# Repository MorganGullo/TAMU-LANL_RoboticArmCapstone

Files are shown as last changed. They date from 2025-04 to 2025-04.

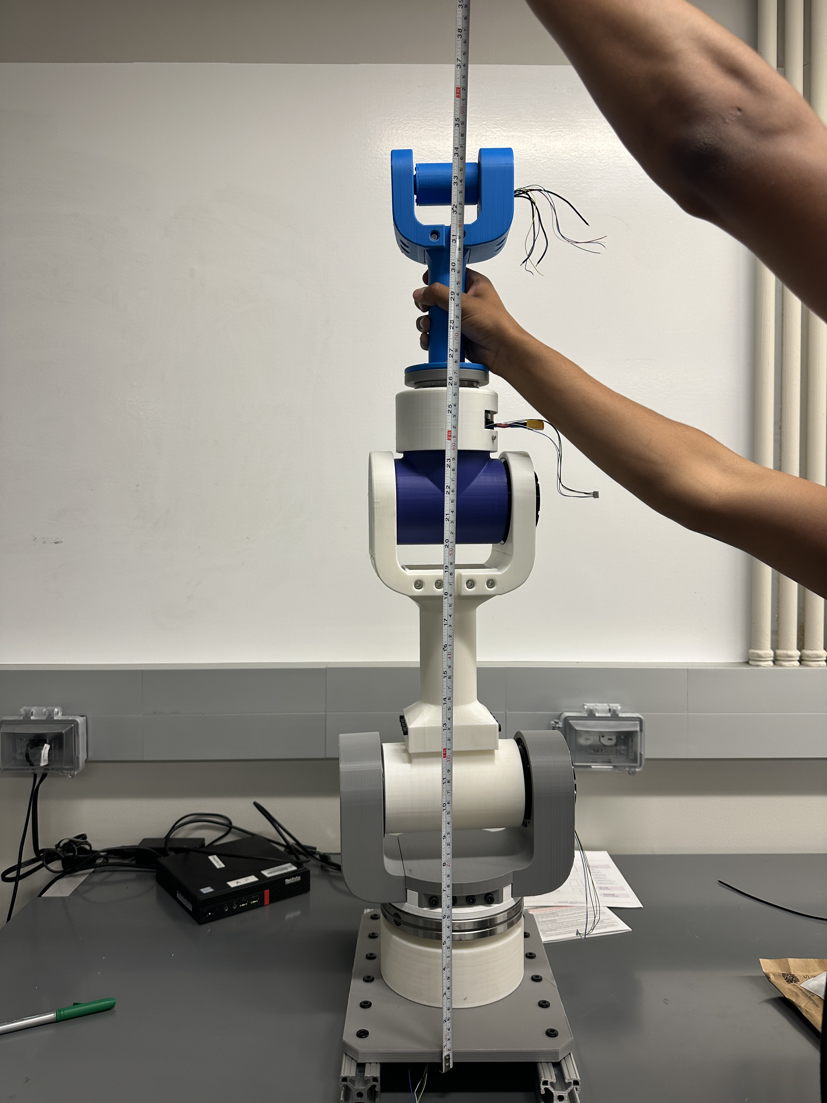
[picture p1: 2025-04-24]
Photos/Vertical Extension.JPG

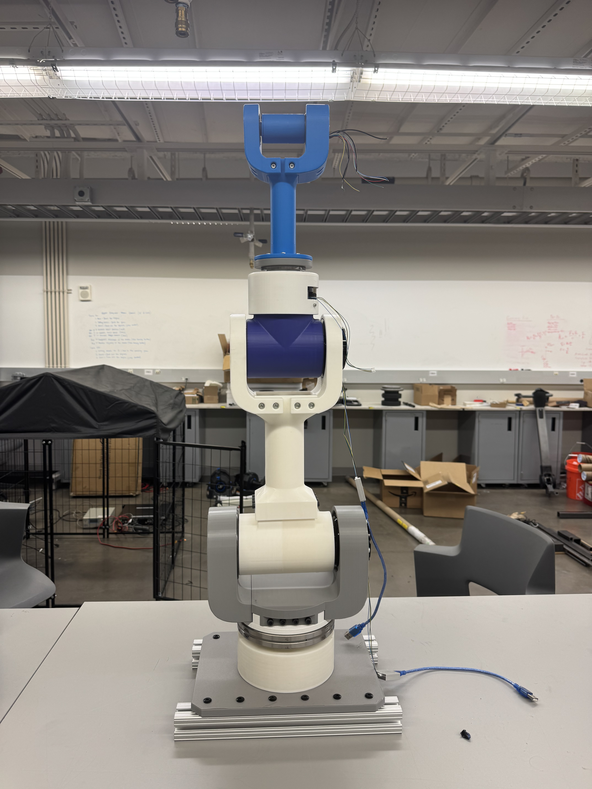
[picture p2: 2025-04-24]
Photos/Vertical Extension.jpeg

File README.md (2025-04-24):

# TAMU LANL Human Robotic Arm Capstone
Texas A&M University Mechanical Engineering Senior Design Project in partnership with Los Alamos National Laboratory to create a Human Robotic Arm Attachment

<p align="center">
  

<p align="center">


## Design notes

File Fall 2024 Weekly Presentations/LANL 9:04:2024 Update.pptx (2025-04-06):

## LANL Team Update 9/3/2024 Izzy Baumler, Dalton Boeckmann, Morgan Gullo, Jade Waldron

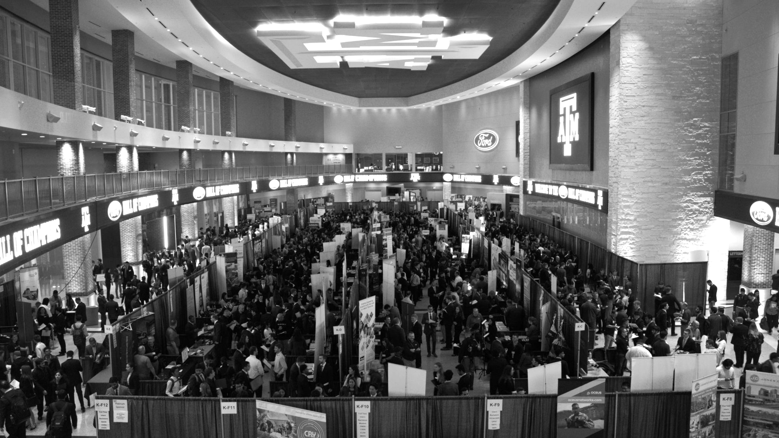
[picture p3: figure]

## Weekly Task Updates

Continuing Research for DR1 Report
- After talking with Dr.Tsenn we have divided up the DR1 research topics
  - Jade - Arm attachments and storage
  - Morgan - Arm attachments and storage
  - Dalton - Dynamic behavior of control arm
  - Izzy - Electrical behavior of control arm
- Meeting with Shuangyu Xie delayed to next tuesday to discuss arm attachment for her weed removal project
- Creating our list of people we want to interview

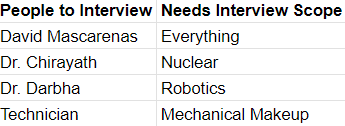
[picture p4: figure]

## Weekly Task Updates

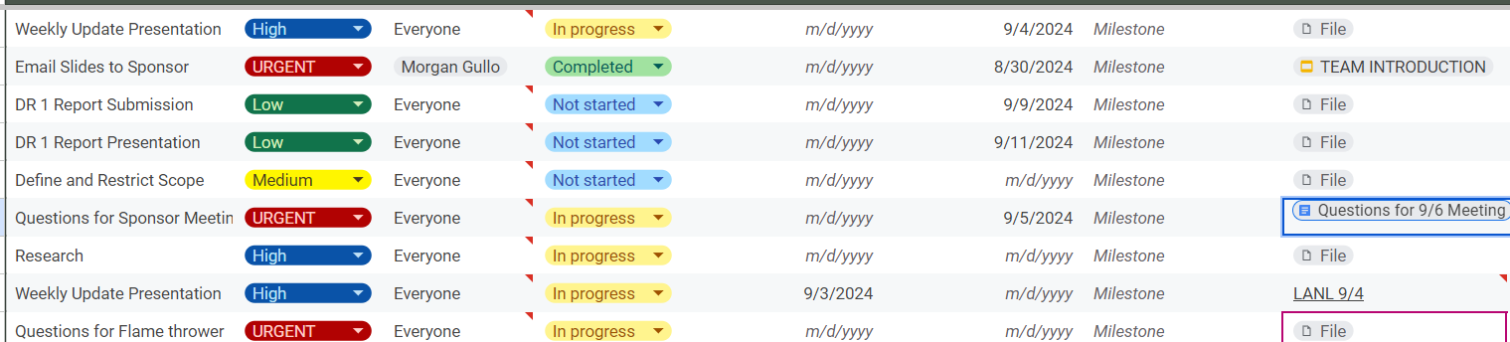
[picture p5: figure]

## Upcoming Week

- Meeting with our sponsor on 9/6 at 1 PM
  - We have prepared questions for him to hopefully answer
- Conducting Interviews for Needs Analysis
- Finalizing and Submitting our DR1 Reports
- Meeting with Shuangyu Xie 9/10

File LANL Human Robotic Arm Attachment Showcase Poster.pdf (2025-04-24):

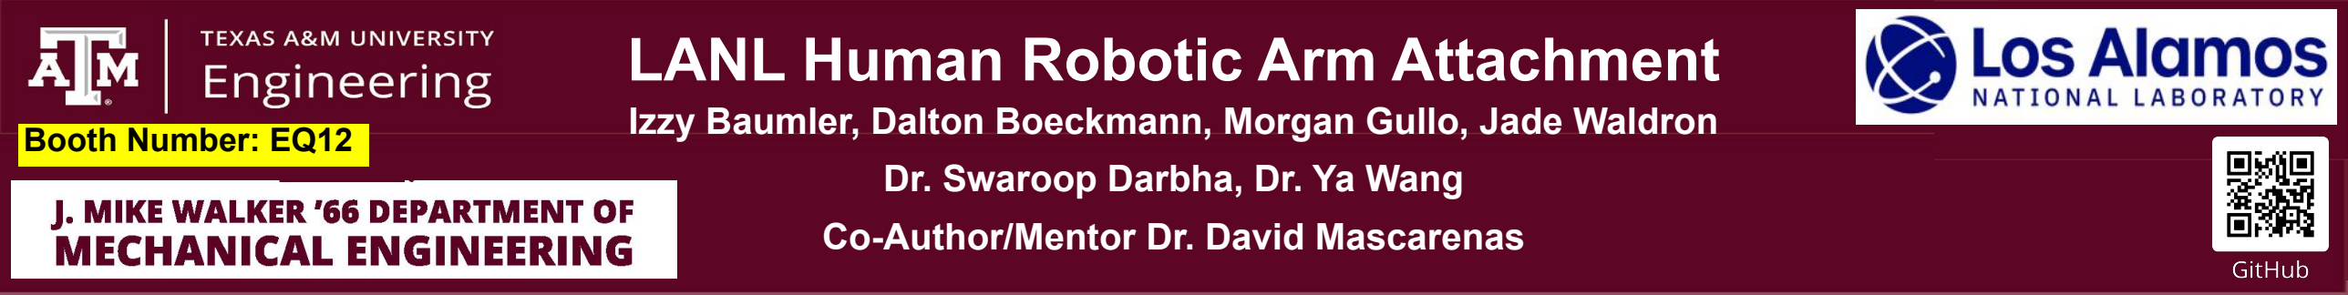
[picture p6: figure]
LANL Human Robotic Arm Attachment; Dr. Swaroop Darbha, Dr. Ya Wang; Co-Author/Mentor Dr. David Mascarenas; Booth Number: EQ12

## Izzy Baumler, Dalton Boeckmann, Morgan Gullo, Jade Waldron

References

[1] Department of Energy. "Hanford Site Overview." U.S. Department of Energy, 2021, https://ecology.wa.gov/waste-toxics/nuclear-waste/hanford-cleanup/hanford-overview.
[2] D. Herman et al., “Evaluation of Technology for Dry Retrieval of Tank Waste,” OSTI OAI (U.S. Department of Energy Office of Scientific and Technical Information), Feb. 2024, doi: https://doi.org/10.2172/2319155.
Acknowledgements

Thank you Dr. David Mascarenas, Dr. Swaroop Darbha, Dr. Ya Wang, RPS, RAD Lab

There is a need for a technology that has 5 degrees-of-freedom and can move through its full range of motion in four degrees-of-freedom of at least 1 Hz.
- The Hanford Site in Washington stores 56+ million gallons of radioactive waste in deteriorating underground tanks. [1]
- Many tanks exceed their lifespan capacity and pose serious environmental and safety risks
- Key challenge: Solidified waste is hard to remove due to small access ports (~1 ft diameter) and extreme radiation levels [2]
- Existing robotic solutions lack the mobility, speed, and/or reliability to operate in confined, hazardous conditions
- Our goal: Design a 5 degrees-of-freedom robotic arm to be eventually mounted on a quadruped robot for effective remote cleaning of nuclear waste tanks

Identified Customer Needs - Derived from interviews with Engineers at Savannah River
National | Laboratory, | supplemental | survey
responses (Robotics Experts), and our sponsor

Only Survey Responses are shown in pie chart*
Design Requirements
- Total system weight: ≤ 14 kg (~30 lbs)
- Minimum Joint Torque (to hold itself up):
- J1 & J2 > 10 Nm, J3 & J4 > 2 Nm
- Reach: ≥ 0.67 meters
- Motion Frequency: ≥ 1 Hz (J1-J4)

Joint 1 SolidWorks Assembly:

Joint 2 SolidWorks Assembly:

Joint 3 SolidWorks Assembly:

The testing process for the robotic arm focused on motor performance under position, speed, and torque control, with testing performed both individually and integrated within the system.
J1 - J4 motors exceeded the target motion frequency of 1 Hz and demonstrated accurate responsiveness to positional commands (0° -
180°). Full-extension load testing on joints J2 and J3 confirmed the arm could sustain torque demands to hold itself up without structural failure, validating the motor selection and mechanical integrity of the design.

Joint 4 SolidWorks Assembly:

Joint 5 SolidWorks Assembly:

Component Selection
- Linkages: 3D printed PLA
- Motors: CubeMars Brushless DC & Gimbal
- Controls: R-link & Upper Computer Software (USB to serial port communication)
- Power Supply: B&K Precision 9115B (80V-60A)
- M6 - M2.5 Various Length Fasteners
Trade Offs:
- Selected Modular Design Instead of Integrated
- Prioritized Speed Instead of Accuracy

Cost Accounting and Cost Model
- Total Spent on Capstone Budget: $4,330
- Total Project Cost Model: $8,370
Our sponsor contributed significantly by providing critical components, including J3 and J4 motors (approx. $700 each) and a power supply (approx. $2,550). The team also incurred an unexpected customs fee of around $500 during motor importation. Future Work & Lasting Impact
- Implement Arduino-to-CAN communication for streamlined multi-motor control and reduced wiring complexity
- Integrate wiring to enable full range of motion
- Develop gimbal-based control for the J5 motor
- The project intends to support ongoing research and spot robot integration
Joint | Calculated Torque (N-m) | Actual Torque (N-m)
J2 | 21.3 | 20
J3 | 3.7 | 2

J1 motor speed response during integrated testing. Verification confirms motion frequency at 1 Hz (6.26 rad/s). *

J1 motor positional response during integrated testing. Verification confirms accurate Position control for (0° - 180°).*

## Problem Statement & Project Motivation

## Customer Needs & Design Requirements

System Design Overview | Design Decisions & Trade Offs

## Testing & Validation

## Budget, Limitations, Impact & Future Work

Metric | Required Values | Verified Values | Units
Weight of the Arm | <14 | 11.88 | kg
Minimum Torque Output | 2-10 | 2-20 | Nm
Reach of Robotic Arm | >0.67 | 0.9 | m
System Mass Distribution | 0.209 | 0.132 | kg/cm
Frequency of Motion | 1 | 1 | Hz

Fully integrated torque testing at maximum extension, comparing the calculated values against the operational torque values to validate that the arm can successfully support itself at full reach. *

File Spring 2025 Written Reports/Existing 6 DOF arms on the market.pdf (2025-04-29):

# Existing 6 DOF arms in Industry

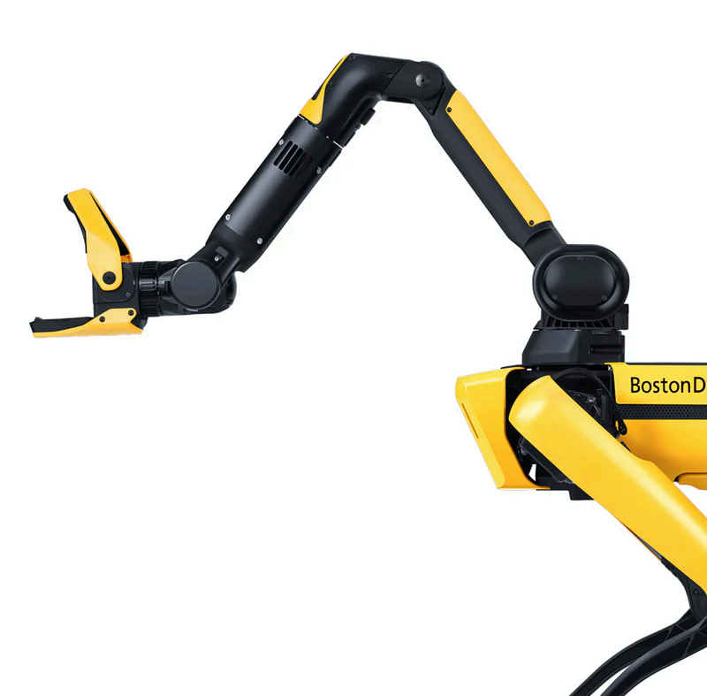
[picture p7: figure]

### Boston Dynamics Spot Arm

- Cost: $65,000
- Weight: 8 kg
- Payload Capability: ~11 kg
- Custom Proprietary BLDC Motors
- Reach ~ 984 mm

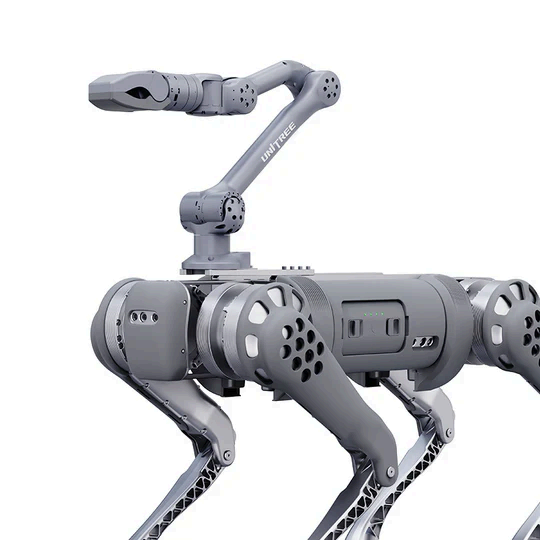
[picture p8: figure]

### Unitree Z1

- Cost: $16,000
- Weight: 4.3 kg
- Payload Capability: ~ 2 kg
- Custom Proprietary BLDC Motors
- Reach ~ 700 mm

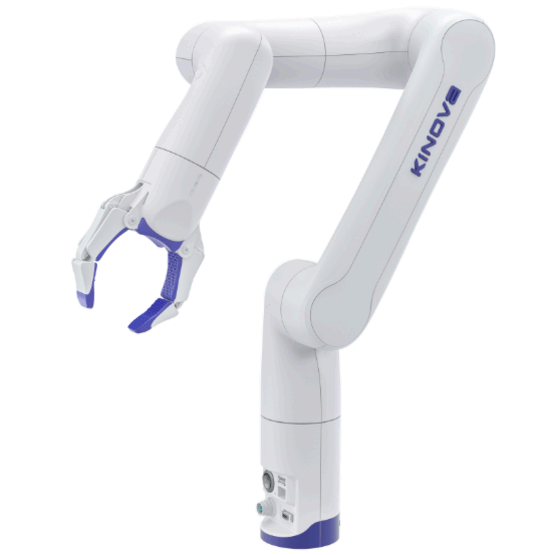
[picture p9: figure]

### Kinova Gen3 lite

- Cost: $13,500
- Weight: 5.4 kg
- Payload Capabilities: ~0.5 kg
- Custom Proprietary BLDC Motors
- Reach ~ 760 mm

# Existing 6 DOF arms in Industry

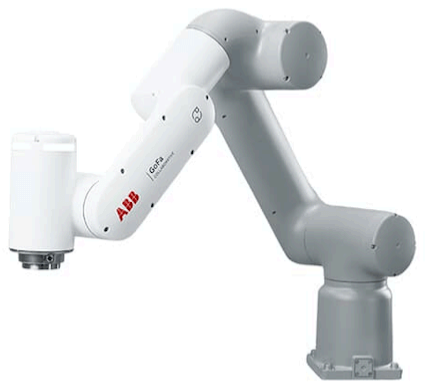
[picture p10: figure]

### ABB CRB15000 GoFa5

- Cost: $38,900
- Weight: 28 kg
- Payload Capabilities: ~5 kg
- Custom Proprietary BLDC Motors
- Reach ~ 1050 mm

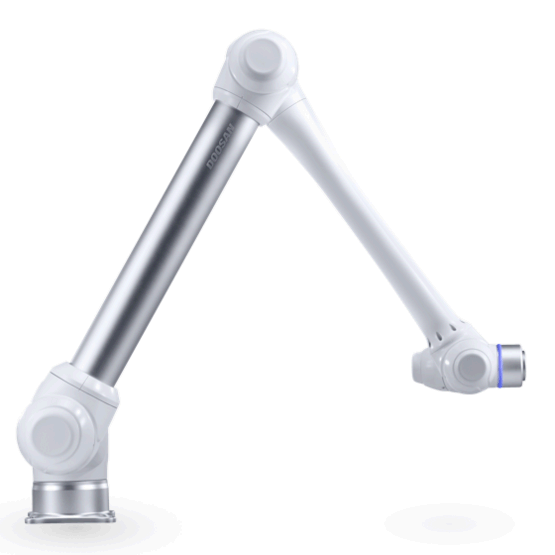
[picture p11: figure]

### Doosan M0617 Collaborative Robot

- Cost: $44,500
- Weight: 34.0 kg
- Payload Capabilities: ~6 kg
- Most likely Servo Motor (built in torque sensing)
- Reach ~ 1700 mm

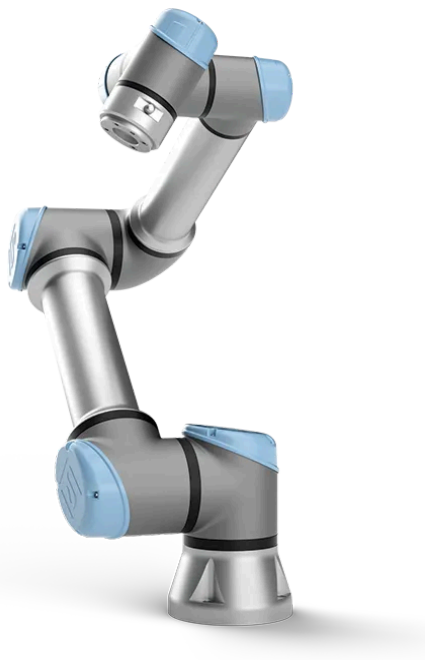
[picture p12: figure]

### Universal Robotics UR5e

- Cost: $36,000
- Weight: 18.4 kg
- Payload Capabilities: ~5 kg
- KBM Frameless AC Servo Motors
- Reach ~ 850 mm

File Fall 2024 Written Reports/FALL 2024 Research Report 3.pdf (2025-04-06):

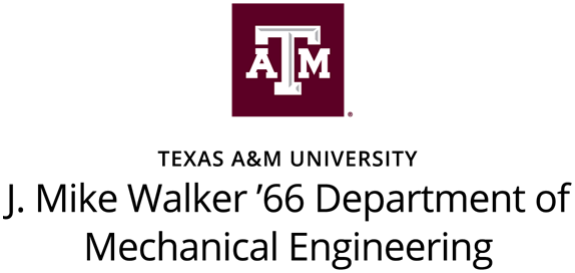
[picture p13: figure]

## Kinematic and Dynamic Considerations for the Design of a 7DoF Robotic Arm for Hazardous Waste Management

### September 4, 2024 Dr. Mascarenas Los Alamos National Laboratory By: Dalton Boeckmann

Glossary

Acronym | Definition
DOE | Department of Energy
LANL | Los Alamos National Laboratory
DoF | Degrees of Freedom
SNPS | Solution Neutral Problem Statement

Table of Contents

### 1. Introduction

The scope of this senior design team's project is to design an advanced robotic solution for hazardous waste removal at the Hanford Site in Washington State. The Hanford Site, among its 45-plus years of plutonium production, has generated more than 56 million gallons of mixed hazardous and radioactive waste. The storage tanks for this waste were designed with a shelf life of 25 years but have already outlived expectation; which has caused more than 68 tanks to be in critical condition. With this increasing issue Los Alamos National Laboratory (LANL) has imposed a design challenge for four mechanical engineering students at Texas A&M university to design a 7 Degree of Freedom (DoF) robotic arm that will attach to a quadruped robot and perform cleaning operations to help break up and remove solidified waste.
The main problem at the Hanford Site is how to address the containment and removal of the nuclear waste, that has already solidified into a crystallized-salt structure. The Department of Energy’s Environmental Impact Statement underlines the disastrous impact of every possible leak of these currently deteriorating tanks by again raising the degree of urgency for ingenious engineering solutions. Historically, the DOE has taken steps to stabilize the Hanford tanks by removing as much liquid waste from the tanks as possible to avoid leakage. [1]
However, recovering the remaining solidified waste is still a formidable technical task. These tanks were not originally designed for waste retrieval process, and the access points are only about one foot in diameter, which greatly restricts the size of equipment that can be used. Furthermore, the high radioactivity calls for remotely operated equipment that many times has failed under harsh conditions inside these tanks. All these challenges have pointed to the need for a solution that is more robust and efficient. The team has been tasked, under the guidance of Dr. David Dennis Lee Mascarenas from Los Alamos National Laboratory, with designing a 7-degreeof-freedom robotic arm attached to a quadruped robot to perform cleaning activities inside these hazardous waste tanks.
Dr. Mascarenas brings expertise in both robotics and environmental remediation needed to address engineering designs to help improve the harsh conditions inside these tanks. Therefore, the robotic arm proposed will be expected to break through the existing barriers of retrieving waste in a more efficient and safe way. This project targets minimizing the risk of further leaks with reduced potential environmental impact by improving the process of waste removal. This design review encompasses the background research done specifically on the design process of the 7 DoF robotic arm, the teams problem statement, and conclusions for future work on the project. First, the background research that follows provides foundational knowledge in current techniques on calculating the kinematic and dynamic behavior of industrial robots in hopes of using it for further application for our specific project.

### 2. Background

There is a great need to introduce design for a 7-DOF robotic arm to effectively meet the needs of expelling waste from hazardous tanks. In light of the success of this design, consideration of the analysis process of the mechanical capability of a 7-DOF arm should be taken into account. This background is necessary in order to provide the grounds where informed design decisions can be made, good control strategies can be initiated, and the integration of advanced technology can be attained.
The goal of this background research is to explain and define the process of analyzing the basic principles of kinematics and dynamics of a 7-DOF robotic arms. More specifically, this will set the grounds for: 1) how the robotic arms end effectors position is described relative to its base location, 2) how possible workspace is defined from these calculations, and 3) how various mathematical calculations are utilized to relate different joint operations and its effects on the endeffectors kinematic and dynamic characteristics. In order to do this, a review of technological developments and their applications in related industries will also be presented with the intent of explaining and applying different advances in robotics to the team’s design. Through this research, the team will gain a better understanding of the necessary design parameters taken into account for a 7-DOF robotic arm that can meet the demands of hazardous waste management cleanup process. Kinematics in robotics starts with analyzing the motion of the system without considering the forces causing these motions. For a 7-degree-of-freedom (7DOF) robot, understanding kinematics is crucial for determining how each joint movement affects the position and orientation of the robot's end-effector. The coordinate systems and reference frames attached to each link are fundamental for modeling a robot's geometry. The Denavit-Hartenberg (DH) convention is a widely-used method for defining these frames and the transformations between them. Denavit-Hartenberg (DH) convention is used to simplify the process of defining and calculating joint and link parameters. The DH convention is a method for assigning coordinate frames to each joint and link of a robot manipulator (see Appendix A). The final DH parameters are then used to form the homogeneous transformation matrices, which describe the position and orientation of the end-effector, in our case the cleaning attachments, relative to the base frame [6]. This convention ensures that despite changes in reference frame assignments, the final transformation matrix remains consistent, making it easier to simplify kinematic equations and understand the end-effector's location.
For a more comprehensive understand there was a recent study done for the design and experimentation of a clamping robot that utilizes a 6DOf system to pick apples off of a tree [3]. The teams started with an analysis of the Denavit-Hartenberg (DH) convention on each of the joints as seen in Figure 1.

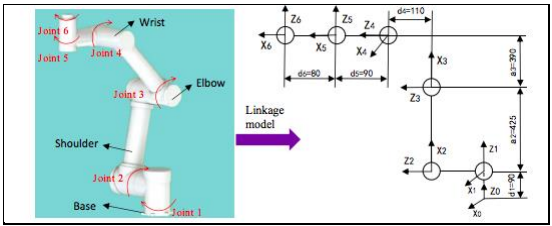
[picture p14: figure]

Figure 1: Linkage Model for Apple Picking Robotic Arm [3]

Through this analysis the team then used the mathematical model explained by the Denavit-Hartenberg (DH) convention to tabulate the results for the four parameters: link length (ai
), link
twist (αi

), joint offset (di

), and joint angle ( θi
). This tabulation can be seen in Table 1.

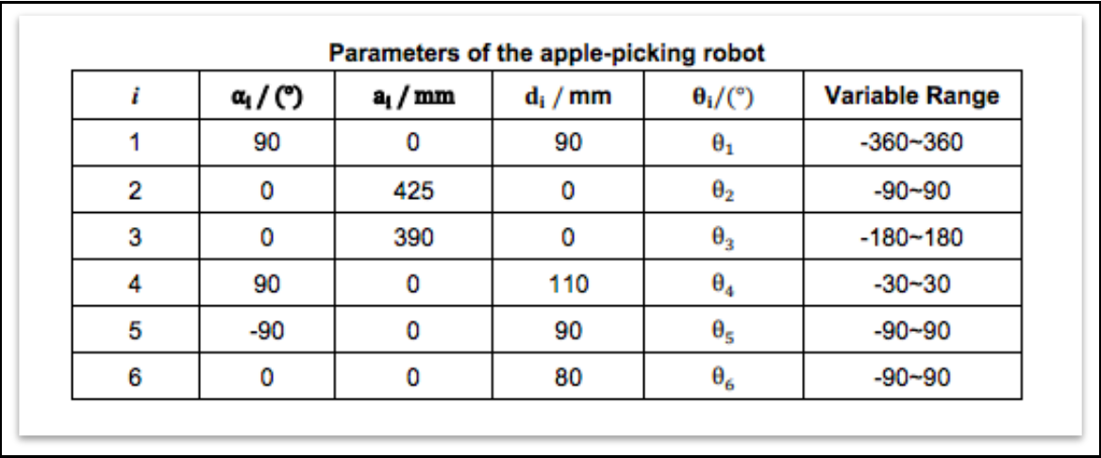
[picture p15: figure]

Table 1: Denavit-Hartenberg Parameters for Apple Picking Robotic Arm [3]

From this study the team then utilized the basics for a homogeneous transformative matrix (See Appendix B), to compute the transformative homogenous matrix with respect to each joint. Through the team utilized a process known to determine the end effectors position and the orientation with respect to the base coordinate system of the robot, so in this example where the robotic arm is connected to ground. This process is called forward kinematics and utilizes the parameters defined by the Denavit-Hartenberg, as seen below:

Equation 1:

Once this transformative matrix was performed with respect to each joint and its Denavit-Hartenberg parameters the forward kinematic calculation was performed to derive a system of equations relating the orientation of the end effector to the bases coordinate system.

Equation 2:

The forward kinematic calculations result in several key outputs: n,o,a, and p each providing crucial information about the end-effector's position and orientation. The matrix output from these calculations includes the position vector p, which specifies the end-effector's location relative to the base frame in 3D space. Specifically, n denotes the direction cosines that align the end-effector's coordinate system with the base frame's axes, while o reflects the rotational offsets. The parameter a represents the link length, which affects the distance between joints and thus the overall reach of the robot. [4] By combining these elements, the transformation matrix provides a comprehensive description of the end-effector’s position and orientation, allowing for a comprehensive analysis of the robot's available workspace [3].
This application is crucial in understanding the design process for the teams 7DOF system robotic end effectors, cleaning tools, position with relativity to its base. From this the team will be able to denote the applicable cleaning space in which the robotic arm attachment will be able to operate and clean. To transition from a task space defined by the Denavit-Hartenberg (DH) convention to an action space (velocity of end effector), there is a mathematical computation used to understand the effects of the joints velocities on its end effectors velocity that will intern control the cleaning time and the dynamic capability of the robot. This can be calculated through a process utilizing a Jacobian Matrix solving process (see Appendix C) [4].
The Jacobian matrix is used to map joint velocities to end-effector velocities, ensuring precise control of the robot's speed and accuracy during operations. The Jacobian matrix helps in defining the cleaning space by indicating how each joint’s motion affects the position and velocity of the end-effector in relation to the robot’s base [7]. This is particularly important for a robot with 7 degrees of freedom, as it offers extra flexibility, known as redundancy, allowing multiple configurations to achieve the same end-effector position and operation [6].
In transitioning from kinematic to dynamic behavior, the Jacobian matrix becomes crucial for force control. It maps joint torques to the forces exerted by the end-effector, enabling the robot to handle delicate cleaning tasks by ensuring controlled force application [6]. This is especially useful when passive force control is employed to prevent damaging the tank walls during cleaning [4]. Additionally, the Jacobian matrix aids in redundancy resolution, helping optimize joint configurations to avoid unnecessary energy use, joint limits, or obstacles in confined spaces like nuclear waste tanks [6].
The significance of this research will become evident as the project progresses. The team will utilize simulation and real-time modeling to analyze the motion of the 7-degree-of-freedom robot arm. Understanding and Utilizing these concepts is not purely theoretical; it forms the basis for optimizing the robot's design parameters, creating efficient control systems, and integrating advanced technologies like passive force control.

### 3. Problem 3.1. Solution Neutral Problem Statement (SNPS):

The solution neutral problem statement (SNPS) is a statement that describes what must be done for the completion of the LANL 7 DoF robotic arm attachment to be successful. Through a comprehensive team analysis, the SNPS was drafted to outline the requirements that need to be met to ensure success. The SNPS is as stated; There should be such a technology that can efficiently manage and remove radioactive waste in extreme operation conditions without causing any damage to the environment or pre-existing containment systems.

### 3.2. Mission Statement:

The team’s mission statement is to design and prototype a robotic power tool arm attachment for the Spot quadruped robot, with cleaning capabilities catered for the removal of nuclear waste from expired tanks. The teams goal is to prevent contamination of local environments, achieve a functional prototype within 8 months, and develop a sustainable solution for the LANL to undergo hazardous waste management processes. This can be seen further outlined in Table 2. The table allows for a overall description of the scope of the project while taking into account various parameters.

Table 2: Outline of the LANL Teams Mission Statement with key influencing Factors

Mission Statement: LANL Power Tool Arm Attachment for a Quadruped Spot Robot

Product Description | Design a Power Tool Arm Attachment with cleaning capabilities
Key Business or Humanitarian Goals | Effectively clean nuclear waste from Nuclear Waste Tanks to prevent contamination of local environments and populations Successfully Prototyped and Fabricate Robotic arm within 8 months
Primary Market | Department of Energy
Secondary Market | US Government, US Military, Nuclear Energy
Assumptions | We can assume: the robot can withstand harsh radioactive environments, the robot can handle large amounts of force without tipping over, the robot can handle large amounts of force without damaging the tank wall, visibility will allow for sensors to determine if plutonium is being removed, we assume the material is a hard tar heel substance
Stakeholders | Washington Citizens, National Research Labs, Department of Energy
Avenues for Creative Design | Cleaning attachments, design of arm movement/control, Semi-Autonomous,
Scope Limitations | Resources, only 4 group members, only 8 months to work on it, No Boston dynamics robotic dog to work with, Size limits, Force limits to protect the tank, Operation limits

### 3.3. Justification of Problem Statement and Mission Statement

Table 3: Justification for the Problem Statement and Mission Statement

Technical Question | Explanation and Justification
1. What is the problem really about? | The problem involves managing and removing hazardous radioactive waste from aging storage tanks at the Hanford Site. The waste has solidified, creating significant environmental and safety risks. The challenge is to design an advanced robotic solution for hazardous waste removal that can efficiently perform this task in a highly radioactive and confined environment.
2. What implicit expectations and desires are involved? | Implicit expectations include the need for a solution that addresses immediate waste management issues while adhering to safety and environmental standards. There is a need for a robotic arm that can operate effectively in harsh conditions and adapt to various ergonomic situations.
3. Are the stated customer needs, functional requirements, and constraints truly appropriate? | Yes, the design must ensure effective waste removal, minimize environmental impact, and operate safely within the tank’s constraints. Constraints such as limited space, high radioactivity, and the need for remote operation are crucial considerations and align with the mission's goals. All of these constraints are appropriate.
4. What avenues are open for creative design? Limitations on scope? | Creative design avenues include exploring innovative on joint movements, translation and rotational devices, control systems, and new waste handling techniques are all potential areas for innovation. Limitations include the project’s 8-month timeframe, 7 DoF design, and the physical constraints of operating within the tank's confined space.
5. What characteristics/properties must the product have (and not have)? | The robotic arm must be easily operatable, precise, and capable of handling nuclear waste The arm should not be overly complex to operate and or fragile.
6. What aspects of the design task can and should be quantified now? | Aspects that can be quantified now, due to the research, include the required torque levels for each joint, an estimation on the maximum force the arm can handle without tipping, the operational workspace, and the speed of action. These parameters are crucial for defining the arm's performance and ensuring it meets the operational requirements for waste removal.
7. Do any biases exist with the chosen task statement or terminology? Has the design task been posed at the appropriate level of abstraction? | The task statement is generally unbiased and appropriately abstract, focusing on the need for an efficient waste management solution without specifying technologies. The only abstract problem the team ran into as the focus on the cleaning tool attachments priority in comparison to the robotic arm, however through Communication with Dr. Mascarenes this was clarified and resolved.
8. What are the technical and technological conflicts inherent in the design task? | Technical conflicts include balancing the arm’s strength and flexibility with size constraints as well as constraints imposed by the quadruped. As well as, the amount pf torque that can be applied so that it doesn’t infringe on the operation of the spot robot. Technological conflicts involve developing a control system capable of handling the arm’s complexity while ensuring that it is easy to operate. Addressing these conflicts requires careful design choices and collaboration with Los Alamos Nation Laboratory and our Sponsor.

### 4. Conclusion

The Texas A&M engineering capstone team has been tasked by the Los Alamos National Laboratory to research, design, and fabricate a 7 Degree of Freedom robotic arm attachment for a quadruped robot to perform hazardous waste management processes. The research encompassed in this report allowed for a comprehensive understanding of the kinematic and dynamic analysis that needs to be made to make precise decisions on the control of arms movement and force applications. It is also important to note that this analysis, will also simplify the process of determining the appropriate; torque levels for each joint, how much applicable force the robot can undergo, the performance space of the robot, and how fast the robot can perform. This research has outlined that the team will begin by analyzing the necessary number of joints for the quadruped robot attachment and use the Denavit-Hartenberg convention to examine the position of the end effector concerning the base, and then calculate and analyze the Jacobian matrices to define the end effectors velocity and the influence the joints torques have on the end effectors dynamic behavior. Research and application of this chosen technique will be verified with LANL professionals to continue to fulfill and meet the goals outlined in this report. Future work will include the continuation of research on the Kinematic and Dynamic Considerations as well as coming together with other group members on their research-specific topics to come together and work towards our end goal. Lastly, the team will ensure the project is on track by continuing weekly meetings with Dr. Mascarenes, emphasizing and adapting areas of focus when needed, and resenting weekly updates.

### 5. Appendices

Appendix A: Denavit-Hartenberg (DH) Convention According to the DH convention, each link and joint is represented by a set of four parameters: link length (ai

), link twist (αi

), joint offset (di

), and joint angle ( θi
). The process begins
with assigning coordinate frames such that the axes zi
), are aligned with the joint axis of each link. If joint i+1 (the joint following the joint being analyzed) is revolute, zi ), is the axis of rotation; if prismatic, zi

is the axis of translation. The base frame is established with its origin on z0and the x0 and y0 axes chosen to form a right-handed system [4]. For each subsequent frame, three cases are considered based on the relative position of zi−1
(the previous joint axis): they may be non-coplanar, parallel, or intersecting. Each case requires specific methods to determine the xi and yi axis to ensure the transformation matrices are accurate [4].

Appendix B: Homogenous Transformative Matrix The homogenous transformative matrix allows for one joint to denote its position with respect to another joint. This understanding is crucial in order to perform forward kinematic calculations.

Appendix C: Jacobian Matrix Calculation The Jacobian Matrix is made up of all the first order partial derivatives of a vector function. On a clearer note, every element that is within the matrix represents a partial derivative of a component of the outputted vector. In the LANL teams case, we would have a 6x7 matrix, due to the rows accounting for the linear and angular velocities, where the columns would represent the joint velocities at each of the 7 joints.

### 5. References

[1] U.S. Department of Energy. (2004). Hanford Site environmental impact statement. Retrieved from https://www.hanford.gov/page.cfm/ERPDraftEIS
[2] Washington State Department of Ecology. (n.d.). *Hanford cleanup*. Washington State Department of Ecology. Retrieved [date you accessed the site], from https://ecology.wa.gov/waste-toxics/nuclear-waste/hanford-cleanup
[3] Guo, J., Wu, W., Liang, Q., & Zhang, Z. (2023). Design and experimentation of a clamping robot for apple picking using 6DOF system. Journal of Field Robotics, 40(3), 512-526. https://doi.org/10.1002/rob.22055
[4] Murray, R. M., Li, Z., & Sastry, S. S. (1994). A mathematical introduction to robotic manipulation. CRC Press.
[5] SpringerLink (Online service) & Siciliano, B. (2009). Robotics: Modelling, planning and control. Springer. https://doi.org/10.1007/978-1-84628-642-1
[6] Siciliano, B., Sciavicco, L., Villani, L., & Oriolo, G. (2009). Robotics: Modelling, planning and control. Springer. https://doi.org/10.1007/978-1-84628-641-9
[7] Craig, J. J. (1986). Introduction to robotics: Mechanics & control. Addison-Wesley Pub. Co..

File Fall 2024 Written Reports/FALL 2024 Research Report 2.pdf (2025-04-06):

# Design Review Report 1

# Integrating Control Systems

# with Boston Dynamics' Spot

# Robot

9/30/24

## Dr. Mascarenas

## Los Alamos National Laboratory

## Izzy Baumler

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
## Introduction

Nuclear waste sites, such as the one at Hanford in Washington State, have reached their shelf life and started to leak leading to land and groundwater contamination—remedial effort involved removing nuclear waste from the tanks at the sites and transferring them into safer containers. The Department of Energy commissioned LANL to find a solution for effective removal. Our senior design project, sponsored by LANL, addresses one aspect of this problem and involves designing an advanced robotic solution for nuclear waste removal.
Located in Washington, the Hanford cleanup is currently underway which is the attempt to clean and repair nuclear storage sites. Starting in the 1940s, nuclear weapons were being produced and with that, a large amount of radioactive and chemical wastes were created. This led to large amounts of land and groundwater contamination by nuclear waste. To remedy this, efforts have begun to remove waste from the tanks and relocate it into safer containers. Currently, the removal process involves “slurrying” the tanks. To achieve this, the tanks are filled with water and drained to remove all of the radioactive waste. This process is inefficient because it requires a lot of water and is very expensive. Our team has been asked to create a 6-degree-of-freedom robotic arm attached to a quadruped robot to clean waste inside the storage tanks. We are working with Dr. Mascarenas from Los Alamos National Labs to achieve our solution. He has provided us with his research on robotic arms and research articles covering the scope of the Hanford cleanup. Additional problems for the nuclear waste removal process have arisen because this waste is stuck to the walls of the tank. This solid waste is a key factor for us to consider when designing a robotic arm. We need to consider creating an arm that is robust enough to withstand forces from cleaning up solid waste.
Our sponsors have identified the quadruped “Spot” robot from Boston Dynamics as the robotic platform on which the arm will be mounted. Our team has divided this project into three areas of research: Arm tool attachments and storage, the dynamic behavior of the arm, and the electrical behavior of the arm. My research area of focus is the electrical behavior of the control arm. To gain a better understanding of the background of the project, I focused on the capabilities of the Boston Dynamics “Spot” robot for the first part of my research.

## Background

Boston Dynamics’ Spot is a quadruped mobile robot that can be used for a variety of tasks from data collection to incident response. Spot is a four-legged robot that can navigate diverse terrain from flat to hazardous. It can be deployed for manual operations, autonomous missions, and can operate without human intervention. Spot has a payload capacity of 14kg, robust API, and comprehensive documentation so it can be tailored to a variety of applications [3]. This makes Spot an ideal vessel to enter the waste tanks and carry the robotic arm to remove nuclear waste. Spot has navigational capability which is enabled by LIDAR technology; this technology allows Spot to map surroundings quickly and accurately [1]. Lidar technology, light detection and ranging, is a three-dimensional laser measurement that allows the surrounding environment to be mapped quickly and accurately. Spot can maneuver unknown, unstructured, or antagonistic environments and can collect various types of data, such as visible images, 3D laser scans, or thermal images. This makes Spot an ideal robot to send into the hazardous environments of the nuclear waste tanks. Spot achieves this through five stereo cameras and greyscale image sensors embedded into the body: two on the front, one on each side, and one on the back. These cameras utilize a textured light projector and project on the ground to indicate stable ground for the robot to place its feet. Spot is programmed to perceive anything above 30 cm in height as an obstacle and walk around it to prevent tipping off balance [3]. Spot has utilized these capabilities in partnership with industries such as construction to carry out dangerous tasks and navigate the terrain of factories and construction sites [3]. This creates efficiency in the work site as well as prevents accidents from occurring.
Control systems and motors for the robotic arm attachment on Spot are critical for the desired functionality of cleaning up nuclear waste. Control systems and motors form the backbone of functionality and precision for robotics. Control systems allow for precise coordination of the arm’s movements, ensuring accuracy in tasks. To create movement in the robotic arm, a control system will need to be utilized. Control systems are crucial for accurately moving the arm to desired positions, maintaining stability, and ensuring precise and smooth operation. The role of the control system is to calculate the joint motor commands that will create the required changes in the robot’s configuration. This process involves solving the inverse kinematics equation, which takes into account the geometry of the arm, its joint limits, and any external forces acting on the system. The control system must continuously adjust motor commands to ensure that the arm responds correctly to both planned and unplanned changes in its environment. This dynamic recalculation is critical for tasks involving real-time adjustments, where precise positioning is essential to the robot's performance.
Inverse kinematics is a fundamental concept in robotics, focusing on determining the necessary joint parameters to achieve a desired position and orientation of the robot’s end effector Unlike forward kinematics, where the end effector's position is derived from known joint parameters, inverse kinematics works in reverse. It calculates the joint angles and positions required to bring the end effector to a specific location in space. The complexity of solving inverse kinematics increases with the number of joints, especially in systems with multiple degrees of freedom, such as robotic arms, where multiple joint configurations may lead to the same end effector position.
Proportional-integral-derivative controllers are used for the most basic joint control operations. They function by reading a sensor, computing the desired actuator output, and summing three input responses to compute the output [2].
Model predictive control (MPC) is a sophisticated control strategy that employs a system model to forecast future behavior over a specified time horizon [4]. However, in tasks such as grinding or welding, which involve physical interaction between the robot and its environment, the implementation of MPC becomes more challenging. This is primarily due to the need for the robot to anticipate the resulting forces and torques. As a result, MPC is not suitable for our solution, as the interaction with unknown materials would render the prediction of forces impractical.
Additionally, motors provide the essential power and motion required for smooth operation, enabling movement at the robot's joints. Robots are frequently deployed in hazardous and high-stakes environments to perform tasks resembling human actions, making it imperative that the motors are precisely matched to these demanding requirements.

## Problem

### Solution Neutral Problem Statement (SNPS)

There should be such a technology that can efficiently remove radioactive waste without causing damage to the environment or pre-existing containment systems.

### Mission Statement

The chart below depicts key aspects we will consider when designing our mission statement.

Mission Statement: LANL Power Tool Arm Attachment for a Quadruped Spot Robot

Product Description | Design a Power Tool Arm Attachment with cleaning capabilities
Key Business or Humanitarian Goals | ● Effectively clean nuclear waste from Nuclear Waste Tanks to prevent contamination of local environments and populations ● Successfully Prototyped and Fabricate Robotic arm within 8 months
Primary | Department of Energy

Market

Secondary Market | ● US Government ● US Military ● Nuclear Energy
Assumptions | We can assume: ● The robot can withstand harsh radioactive environments ● The robot can handle large amounts of force without tipping over ● The robot can handle large amounts of force without damaging the tank wall ● Visibility will allow for sensors to determine if plutonium is being removed ● We assume the material is a hard tar heel substance
Stakeholders | ● Washington Citizens ● National Research Labs ● Department of Energy
Avenues for Creative Design | ● Cleaning attachments ● Design of arm movement/control ● Semi-Autonomous
Scope Limitations | ● Resources ● 4 group members ● 8 months to work ● No Boston Dynamics robot dog to experiment with ● Size limits ● Force limits to protect the tank ● Operation limits

The problem is really about keeping the citizens of Hanford Washington safe by cleaning up the hazardous nuclear waste being stored in bins. Hanford has produced two-thirds of the plutonium used in US nuclear weapons stockpiles. The implicit expectations and desires of our project involve human-like dexterity to achieve six degrees of freedom. Haptic feedback and remote control allow the robotic arm to be controlled from a distance with real-time sensory information. Operational efficiency in confined spaces is essential for our project to operate within the confined spaces of the waste containers. Tool compatibility ensures seamless integration with cleaning equipment. Passive force control is crucial for allowing the robotic arm to interact with the tank walls without causing damage and creating more radiation leaks. Finally, minimal human intervention is needed because the robot will be operating in a highly radioactive and dangerous environment. Currently, we have not explored all avenues of possible solutions. The customer needs and constraints seem appropriate for the proposed solution, but we cannot be certain until all possible solutions are researched further. One constraint that may not be appropriate is a robotic arm with seven degrees of freedom. We might be able to create a functional solution that requires less degrees of freedom. Three main avenues we have identified for creative design and inventive problem solving are the tool exchange system, force actuator, and the feedback system on the end of the robot. These are all aspects that can contribute to protecting the wall of the container the waste is stored in. We need inventive problem-solving to remove waste from the wall without damaging the wall and allowing even more radiation to seep through. One of the main limitations of the scope of our robot is that the payload must be able to attach to aluminum payload rails. These rails can accept T-slot nuts such as Misumi HNTR5-5. Because we are using this frame to attach our payload, we must ensure that the mounting screws do not project more than 6.3 mm below the top surface of the mounting rail and that the T-slot nuts are fully supported along each edge.
The product must possess 6 degrees of freedom for high flexibility and dexterity. It should be able to easily mount on the Spot robot through attachment to the aluminum payload rails. Our design should create a seamless integration between the Spot robot and our robotic arm. The design must support multiple attachments, such as grinders, wire wheels, drills, vibratory cutters, and sanders, to perform various tasks to clean up waste. Passive force control is essential for safe and precise operation in the sensitive environments of the tanks. Additionally, the product must adhere to the specific parameters and dimensions required for compatibility with the Spot robot.
Our product must ensure it does not damage the container walls during cleaning tasks while being compact enough to fit on the Spot robot using the aluminum payload rails. Additionally, the force and torque generated by the arm attachment must not cause the Spot robot to tip over during operation.
Given the open-ended nature of the project, certain design aspects cannot be quantified at this stage. One inherent limitation is the use of the Boston Dynamics Spot robot as the platform for our robotic arm, despite the possibility that other quadruped robots may be better suited for navigating the hazardous terrain within storage tanks.
The design task involves several technical challenges, including the need for the robot to operate semi-autonomously via remote control, requiring a complex control system not typically covered in mechanical engineering coursework. Another concern is the potential impact of radioactive materials on the arm and robot components, raising issues related to durability and safety. There is not a lot of research available on the effects of nuclear waste on the storage tanks which means our solution needs to be carefully thought out. The robot's cleaning capability is also restricted by the tank depth, limiting access to about 5 feet from the ground. Moreover, the system is designed to handle tanks with minimal liquid or sludge plutonium, focusing on removing tar-like substances adhered to the walls. Limited visibility during operation further complicates control, highlighting the need for an intuitive design and user-friendly control system to enhance maneuverability and effectiveness.

## Conclusions

This project aims to ensure the safety of Hanford, Washington by addressing the cleanup of hazardous nuclear waste. Our robotic arm must achieve human-like dexterity to perform intricate tasks. This arm must integrate seamlessly with the Spot robot by adhering to specific dimensions and payload constraints. Our project faces the challenges of needing a sophisticated control system to navigate the tank’s depth and visibility. Boston Dynamics’ Spot is a versatile quadruped robot capable of navigating various terrains, from flat surfaces to hazardous environments. To effectively integrate a robotic arm with Spot, understanding control systems and motors is crucial. Control systems ensure accurate coordination and smooth operation of the arm.

## References/Citations

[1] Buhren, Michael. “Lidar-on-a-chip.”

https://www.muensterland.com/en/economy/business-location/innovations/technology-scouting/te

ch-compass/engineering-pro/robotics/lidar/.

[2] Goodwin, Graham C., et al. “The PID Controller & Theory Explained - NI.” National Instruments, 8

July 2024, https://www.ni.com/en/shop/labview/pid-theory-explained.html. Accessed 9

September 2024.

[3] “Spot.” Boston Dynamics, https://bostondynamics.com/products/spot/. Accessed 9 September 2024.
[4] “What is Model Predictive Control? - MATLAB & Simulink.” MathWorks,

https://www.mathworks.com/help/mpc/gs/what-is-mpc.html. Accessed 9 September 2024.

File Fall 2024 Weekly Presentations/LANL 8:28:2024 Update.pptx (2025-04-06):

## LANL Team Update 8/28/2024 Izzy Baumler, Dalton Boeckmann, Morgan Gullo, Jade Waldron


## Project Context

- The Hanford site in southeast Washington was created in 1943 to produce plutonium for the Manhattan Project, supplying two-thirds of the plutonium in US nuclear weapons.
- Around 60 square miles of groundwater at Hanford are still contaminated above federal standards, with no active nuclear production but ongoing cleanup.
- A Quadruped robot will be entering these containers to clean up and remove waste

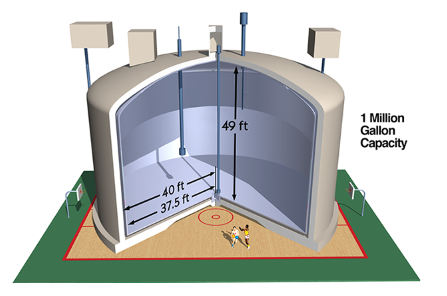
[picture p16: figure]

## Weekly Task Updates

- Created team introduction presentation
- Currently reading through all research papers that sponsor provided us
- Met with sponsor for one hour to gain a better knowledge of the project scope
  - Created task list to achieve by Friday
- Set weekly meeting time for Fridays at 1 PM
- Meeting with MEEN Professor Xie to get a demo of Spot Robot

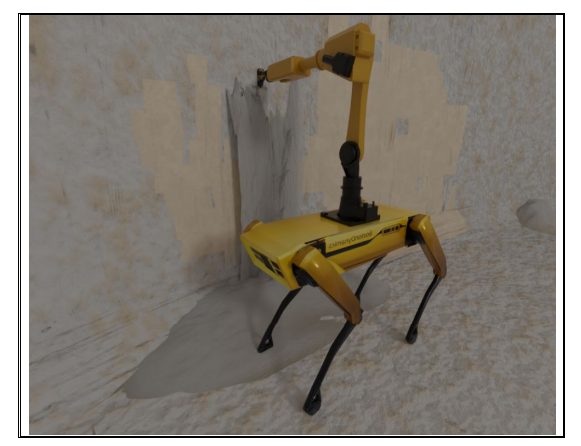
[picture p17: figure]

## Upcoming Week Slides

- 2nd Meeting with Sponsor to present our individual interest and ideas
- Work with sponsor to restrict the Scope of our Project and its requirements
- Collaborate as a Team to delegate roles and responsibilities due to team reorganization
- Continue research about Dry Retrieval and Hanford Cleanup

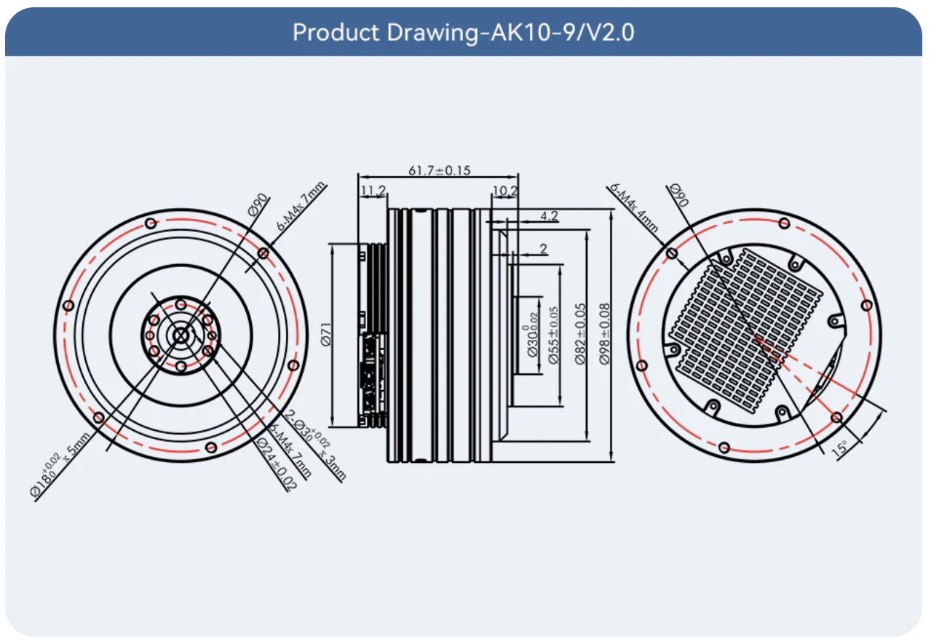
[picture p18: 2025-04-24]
Motor Specifications/J1 and J2/Motor Dimensions.png

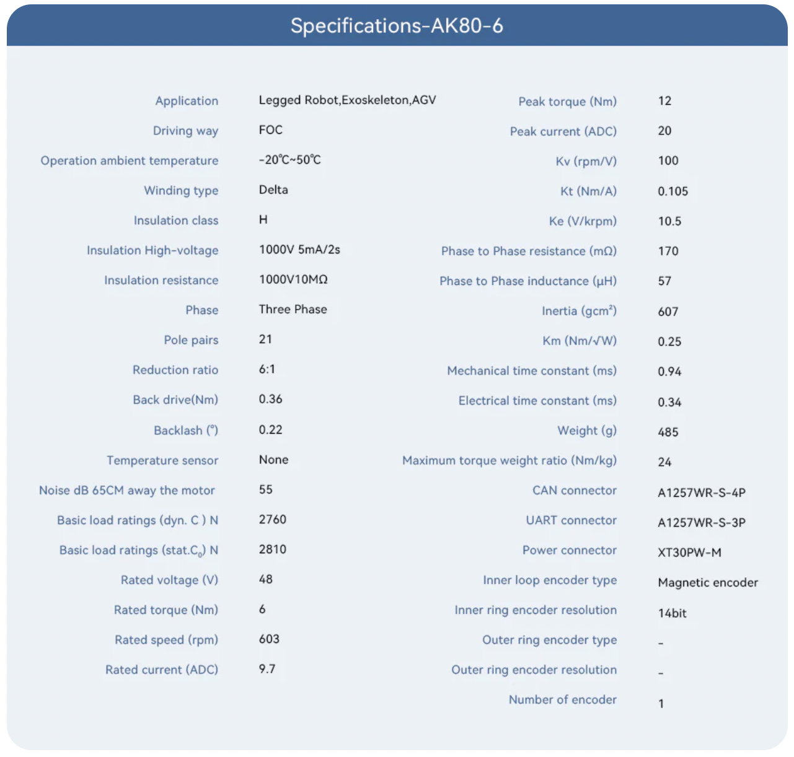
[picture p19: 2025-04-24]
Motor Specifications/J3 and J4/Specifications.png

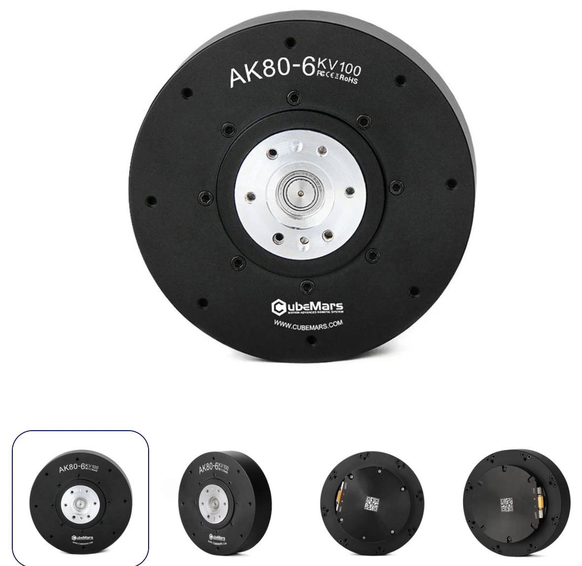
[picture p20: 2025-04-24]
Motor Specifications/J3 and J4/Motor Image.png

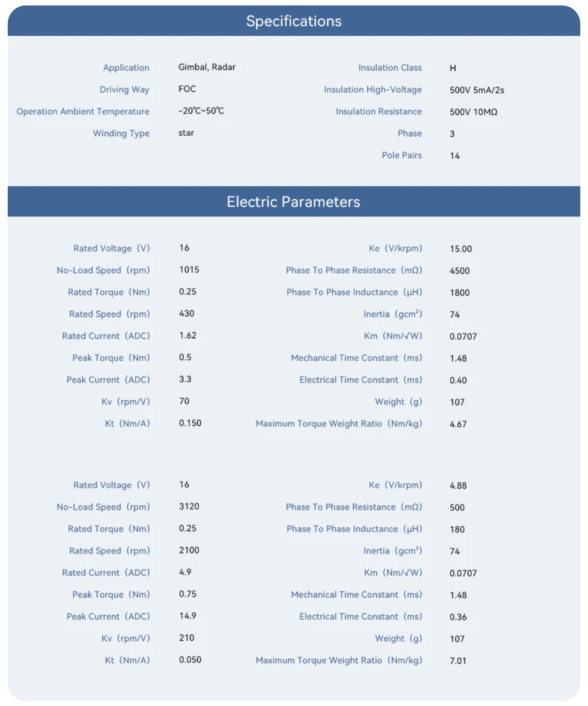
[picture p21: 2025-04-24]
Motor Specifications/J5/Specifications and Electrical Parameters.png

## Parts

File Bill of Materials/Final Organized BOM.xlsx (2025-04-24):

Requestor | David Mascarenas
Justification: | Need these components to build the Human Robotic Arm Attachment
Code:
Needed by: | ASAP
 |  | Hand tools
Group | Izzy Baumler, Dalton Boeckmann, Morgan Gullo, Jade Waldron
Budget Analyst | Morgan Gullo
Cost Center
McMaster-Carr
Part | Part Number | Vendor | Cost each | Qty | Total Cost | Notes | Restrictions? | URL
J1 Bearing | 2010N16 | McMaster-Carr | $514.58 | 1 | $514.58 | 80mm shaft High-Load Face-Mount Crossed-Roller Bearing |  | https://www.mcmaster.com/2010N16/
J2 Bearing | 5972K3 | McMaster-Carr | $46.38 | 1 | $46.38 | 60mm shaft Ball Bearing |  | https://www.mcmaster.com/5972K3/
J3 Bearing | 5972K113 | McMaster-Carr | $36.12 | 1 | $36.12 | 55mm shaft Ball Bearing |  | https://www.mcmaster.com/5972K113/
J4 Bearing | 4471N14 | McMaster-Carr | $586.42 | 1 | $586.42 | Face-mount Crossed-Roller Bearing |  | https://www.mcmaster.com/4471N14/
J5 Bearing | 5972K105 | McMaster-Carr | $13.12 | 1 | $13.12 | 20mm shaft Ball Bearing |  | https://www.mcmaster.com/5972K105/
M6 Heatset Inserts | 94180A371 | McMaster-Carr | $13.80 | 3 | $41.40 | M6 x 1 mm Thread Size, 7.6 mm Installed Length |  | https://www.mcmaster.com/94180A371/
M5 Heatset Inserts | 94180A361 | McMaster-Carr | $17.86 | 2 | $35.72 | M5 x 0.8 mm Thread Size, 6.7 mm Installed Length |  | https://www.mcmaster.com/94180A361/
M4 Heatset Inserts | 94180A351 | McMaster-Carr | 21.82 | 1 | $21.82 | M4 x 0.7 mm Thread Size, 4.7 mm Installed Length |  | https://www.mcmaster.com/94180A351/
M3 Heatset Inserts | 94180A331 | McMaster-Carr | $20.44 | 1 | $20.44 | M3 x 0.5 mm Thread Size, 3.8 mm Installed Length |  | https://www.mcmaster.com/94180A331/
M4 x 15mm Fastener | 90128A332 | McMaster-Carr | $9.71 | 1 | $9.71 | M4 x 0.7 mm Thread, 15 mm Long |  | https://www.mcmaster.com/90128A332/
M6 x 18mm Fastener | 91290A323 | McMaster-Carr | $19.58 | 1 | $19.58 | Black-Oxide, M6 x 1 mm Thread, 18 mm Long |  | https://www.mcmaster.com/91290A323/
M5 x 30mm Fastener | 91290A194 | McMaster-Carr | $5.74 | 1 | $5.74 | Black-Oxide, M5 x 0.8 mm Thread, 30 mm Long, Fully Threaded |  | https://www.mcmaster.com/91290A194/
M4 x 10mm Fastener | 91274A117 | McMaster-Carr | $5.28 | 1 | $5.28 | M4 x 0.7 mm Thread, 10 mm Long |  | https://www.mcmaster.com/91274A117/
M5 x 22mm Fastener | 91290A248 | McMaster-Carr | $12.08 | 1 | $12.08 | Black-Oxide, M5 x 0.8 mm Thread, 22 mm Long |  | https://www.mcmaster.com/91290A248/
M6 x 10mm Fastener | 91290A316 | McMaster-Carr | $15.13 | 1 | $15.13 | Black-Oxide, M6 x 1 mm Thread, 10 mm Long |  | https://www.mcmaster.com/91290A316/
M4 x 10mm Fastener | 90128A212 | McMaster-Carr | $9.49 | 1 | $9.49 | M4 x 0.7 mm Thread, 10 mm Long |  | https://www.mcmaster.com/90128A212/
M4 x 6mm Fastener | 90128A208 | McMaster-Carr | $10.42 | 1 | $10.42 | M4 x 0.7 mm Thread, 6 mm Long |  | https://www.mcmaster.com/90128A208/
M5 x 8mm Fastener | 91290A222 | McMaster-Carr | $12.75 | 1 | $12.75 | Black-Oxide, M5 x 0.8 mm Thread, 8 mm Long |  | https://www.mcmaster.com/91290A222/
M3 x 5mm Fastener | 92095A177 | McMaster-Carr | $7.39 | 1 | $7.39 | Passivated 18-8 Stainless Steel, M3 x 0.50 mm Thread, 5mm Long |  | https://www.mcmaster.com/92095A177/
Amazon
Part | Part Number | Vendor | Cost each | Qty | Total Cost | Notes | Restrictions? | URL
30 Small Drawer Modular Storage System | CRAFTSMAN Storage Organizer | Amazon | $20.98 | 1 | $20.98 | Used to organize and label fasteners |  | https://www.amazon.com/Craftsman-CMST40730-SMALL-DRAWER-ORGANIZER/dp/B09BDKWRS3
Robot Safety Cage | Outdoor Dog Kennel | Amazon | $159.99 | 1 | $159.99 | 4'L x 4'W x 4.5'H |  | https://www.amazon.com/Kennel-Outdoor-Large-Outside-Enclosures/dp/B0BTHJ6LZT
Aluminum Extrusion Slots | T-nut Slots | Amazon | $15.49 | 1 | $15.49 | 20PCS 4040 Series M6 T-Nut |  | https://www.amazon.com/Sliding-Aluminum-Extrusion-Profile-8mm%EF%BC%884040-M6/dp/B08MT4DGXN?th=1
Aluminum Extrusion Fastners | Black Flat Head Allen Head Joint Connecting Bolts | Amazon | $7.99 | 1 | $7.99 | 12-Pack M6 x 22mm |  | https://www.amazon.com/cSeao-12-Pack-Conecting-Furniture-Stainless/dp/B0CGMX7TP3
Fastener Tool | T-Key Allen Wrench Set | Amazon | $14.46 | 1 | $14.46 | 8pc set Metric MM sizes 2-10 |  | https://www.amazon.com/Eklind-35198-Piece-Standard-T-Keys/dp/B0015SIUCQ?gQT=1
USB Port Extension | IVETTO Brand | Amazon | $19.99 | 1 | $19.99 | 7-port USB port |  | https://www.amazon.com/IVETTO-Individual-Switches-MacBook-Surface/dp/B08R86STK4?hvadid=80882933901292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
M2.5 Heatset Inserts | Hanglife Store | Amazon | $8.99 | 1 | $8.99 | Heat-set Threaded Inserts M2.5 |  | https://www.amazon.com/HANGLIFE-Heat-Set-Threaded-Printing-Components/dp/B0CS6YVJYD?s=hi
Power Supply Testing Cable | XT30 to Orings | Amazon | $6.39 | 1 | $6.39 | 14AWG Silicon Cable XT30 to O Ring Terminal Cable |  | https://www.amazon.com/PNGKNYOCN-Silicon-Terminal-Terminals-Extension/dp/B0CGTW8C4S
Terminal Block | Dual Row Screw Terminal Strip | Amazon | $12.09 | 2 | $24.18 | Terminal Block 6 Position 600V 100A |  | https://www.amazon.com/Sscon-Dual-Rows-Terminal-Block/dp/B07V4J5WK8?th=1
Motor to Power Supply Cable | XT60 to Orings | Amazon | $13.27 | 5 | $66.35 | 12 AWG 1.5 M |  | https://www.amazon.com/SinLoon-Terminal-23-6inch-Connector-Aircraft/dp/B0C964KCQF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
Power Cable Converter | Converter | Amazon | $4.69 | 2 | $9.38 | XT30F to XT60M |  | https://www.amazon.com/DKARDU-Adapter-Female-Battery-Charger/dp/B0CZHR1N8R?s=industrial
Power Supply to Terminal Block Cable | Battery Cable | Amazon | $25.99 | 1 | $25.99 | 6 AWG 5 feet |  | https://www.amazon.com/Battery-Copper-Inverter-Automotive-Motorcycle/dp/B0D44JVG2T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
Wire Mesh | Cable Mesh | Amazon | $7.63 | 1 | $7.63 | 10 ft 1/2 inch |  | https://www.amazon.com/Alex-Tech-10ft-Protector-Sleeving/dp/B07FW3GTXB?sp_csd=d2lkZ2V0TmFtZT1zcF9hdGY
J1 and J2 Motor | AK10-9 V2.0 KV100 | Amazon | $798.90 | 2 | $1597.80 | Brushless DC Motor with installed driver board | Bought by Tmotor shop within Amazon; Page was taken down soon after purchase; Link provided from CubeMars for total price of $798.90 | https://store.cubemars.com/products/ak10-9-v2-0-kv100?variant=41060705894494
J5 Motor | GL40 KV70 | Amazon | $97.99 | 1 | $97.99 | Gimbal Motor with installed encoder | Bought by Tmotor shop within Amazon; Page was taken down soon after purchase; Link provided from CubeMars for total price of $97.99 | https://store.cubemars.com/products/gl40-kv70
Soldering Tips | Heat Set Insert Tool Tips | Amazon | $9.99 | 1 | $9.99 | Tips for Threaded inserts M2 M2.5 M3 M4 M5 M6 |  | https://www.amazon.com/Tips-Soldering-Iron-Compatible-Components/dp/B0DB1SSKVN?hvadid=580995206543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
RobotShop
Part | Part Number | Vendor | Cost each | Qty | Total Cost | Notes | Restrictions? | URL
J3 and J4 Motor | AK80-6 KV100 | Robotshop | $712.90 | 2 | $1425.80 | Brushless DC Motor with installed driver board | Can be bought on CubeMars for $569.90 but only through Paypal | https://www.robotshop.com/products/cubemars-cubemars-ak80-6-kv100-brushless-dc-motor-robot-w-large-torque-high-integration
Debugging tool for AK Motors | CubeMars R-link V2.0 | RobotShop | $51.90 | 4 | $207.60 | Can be controlled through Upper Computer provided by CubeMars | Can be bought on CubeMars for $39.90 but only through Paypal | https://www.robotshop.com/products/cubemars-cubemars-r-link-v20-debugging-tool-ak-motors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
Univeristy/Sponsor Inventory
Part | Part Number | Vendor | Cost each | Qty | Total Cost | Notes | Restrictions? | URL
Power Supply | 9115B/08AK4948 | Newark | $2550.00 | 1 | $2550.00 | 80V, 60A |  | https://www.newark.com/b-k-precision/9115b/power-supply-programmable-1-output/dp/08AK4948
4040 T-slot Aluminum Extrusion | 350 millimeter | FEDC | $9.75 | 2 | $19.50 |  |  | https://www.amazon.com/Seekliny-Aluminum-Extrusion-T-Slotted-Accessories/dp/B0D5QP42L5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
3D Printed Parts | Printed using PLA | RPS | N/A | N/A
M6 x 20mm | N/A | RPS | $9.99 | 1 | $9.99 |  |  | https://www.amazon.com/Kozelo-50pcs-Socket-Head-Screws/dp/B0DDJBL5YG?sp_csd=d2lkZ2V0TmFtZT1zcF9hdGY
Soldering Iron | Used to insert heatset inserts into PLA parts | RPS | $16.99 | 1 | $16.99 |  |  | https://www.amazon.com/Soldering-Digital-Ceramic-Adjustable-Temperature/dp/B0C2Z1WNRV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
M3 x 4mm | N/A | RPS | $6.99 | 1 | $6.99 |  |  | https://www.amazon.com/uxcell-M3x4mm-Thread-Button-Socket/dp/B01AXURZP4
M4 x 8mm | N/A | RPS | $11.89 | 1 | $11.89 |  |  | https://www.amazon.com/M4-0-70-Button-Stainless-Fullerkreg-Plastic/dp/B07H17CPS3
M6 Washers | N/A | RPS | $4.99 | 1 | $4.99 |  |  | https://www.amazon.com/LUPANTER-Washers-Stainless-Metric-Screws/dp/B0CNMZTDN4?sp_csd=d2lkZ2V0TmFtZT1zcF9hdGY
M6 Hex Nuts | N/A | RPS | $9.99 | 1 | $9.99 |  |  | https://www.amazon.com/ZQZ-M6-1-0mm-Hex-Nuts-Stainless/dp/B0CQJHZ5BW?sp_csd=d2lkZ2V0TmFtZT1zcF9hdGY
M2.5 x 6mm | N/A | RPS | $7.29 | 1 | $7.29 |  |  | https://www.amazon.com/DTGN-M2-5-0-45x6mm-Button-Socket-Screws/dp/B0DNMV96KX?sp_csd=d2lkZ2V0TmFtZT1zcF9hdGY
M2.5 x 5mm | N/A | RPS | $7.19 | 1 | $7.19 |  |  | https://www.amazon.com/Button-Socket-Screws-Stainless-Bright/dp/B08HYLLX7C
M4 washers | N/A | RPS | $4.99 | 1 | $4.99 |  |  | https://www.amazon.com/Washer-Stainless-Steel-Washers-100PCS/dp/B0BGH6YLB7?sp_csd=d2lkZ2V0TmFtZT1zcF9hdGY
M4 Hex Nuts | N/A | RPS | $9.99 | 1 | $9.99 |  |  | https://www.amazon.com/ZQZ-M4-0-7mm-Stainless-Hardware-Standard/dp/B0CQJJV8Q8?sp_csd=d2lkZ2V0TmFtZT1zcF9hdGY
 |  |  |  | Customs Fee | $514.41
 |  |  |  | Shipping | $51.28
 |  |  |  | Total | $8376.05

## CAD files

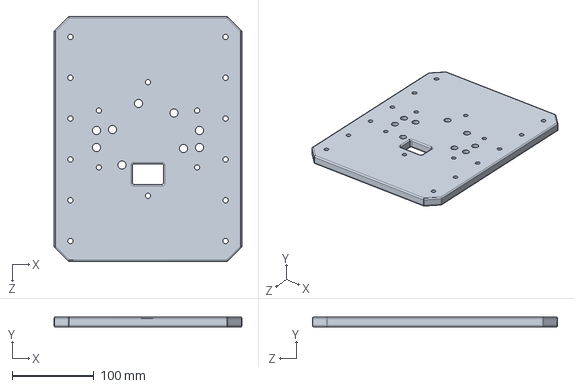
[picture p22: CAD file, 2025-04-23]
SolidWorks Files/Base/Robot Base.SLDPRT
230.0 x 12.7 x 300.0 mm

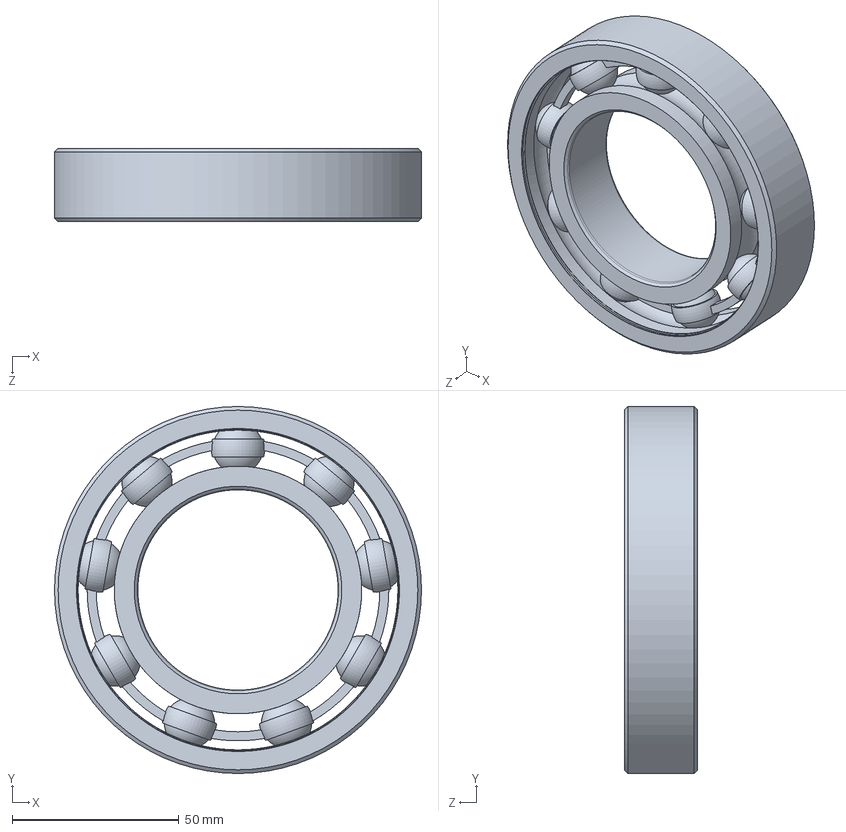
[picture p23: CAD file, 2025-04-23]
SolidWorks Files/Joint 2/J2 Ball Bearing (K972K3).SLDPRT
110.0 x 110.0 x 22.0 mm

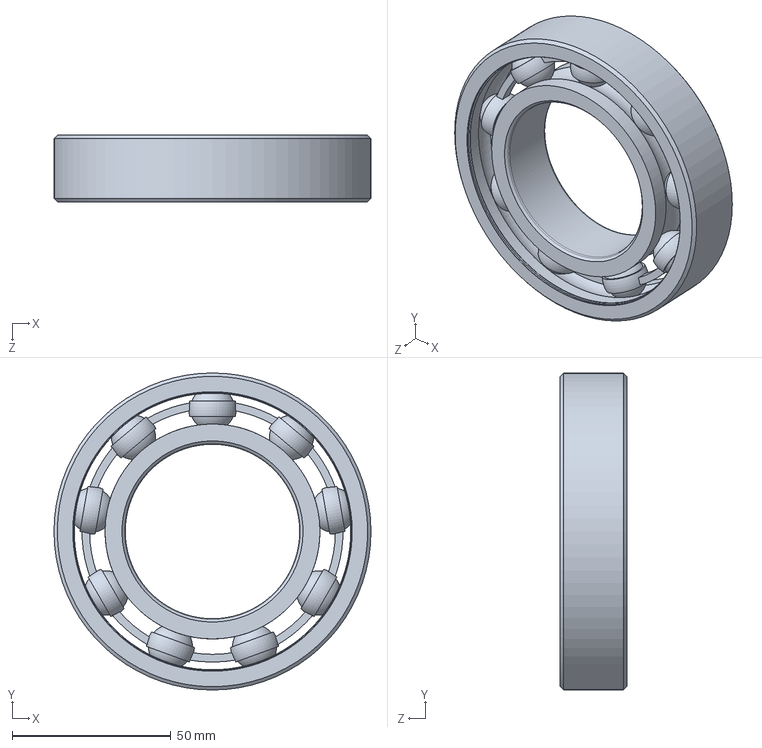
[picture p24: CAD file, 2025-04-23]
SolidWorks Files/Joint 3/J3 Ball Bearing (5972K113).SLDPRT
100.0 x 100.0 x 21.0 mm

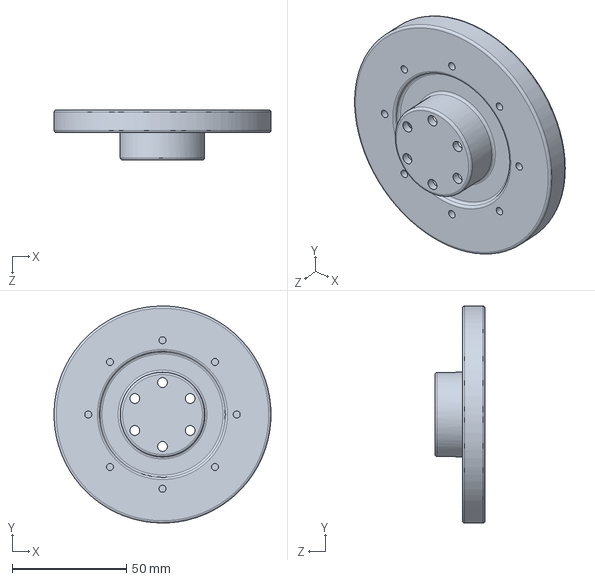
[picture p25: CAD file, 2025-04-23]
SolidWorks Files/Joint 4/J4 Mushroom Cap.SLDPRT
95.0 x 95.0 x 22.0 mm

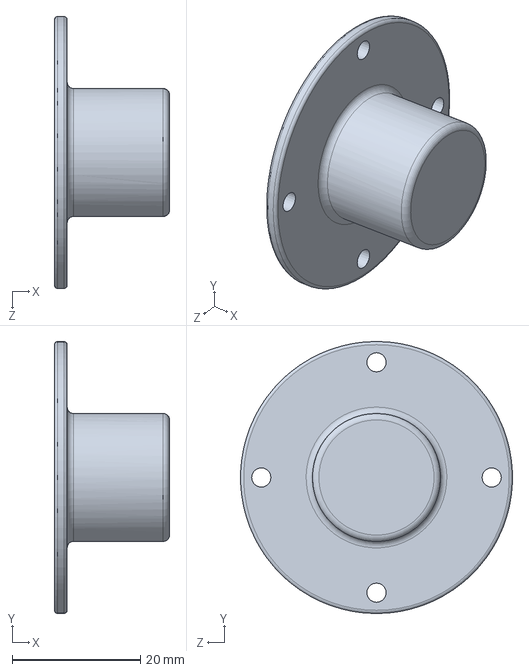
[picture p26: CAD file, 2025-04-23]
SolidWorks Files/Joint 5/J5 Cylinder Cap.SLDPRT
18.0 x 42.5 x 42.5 mm

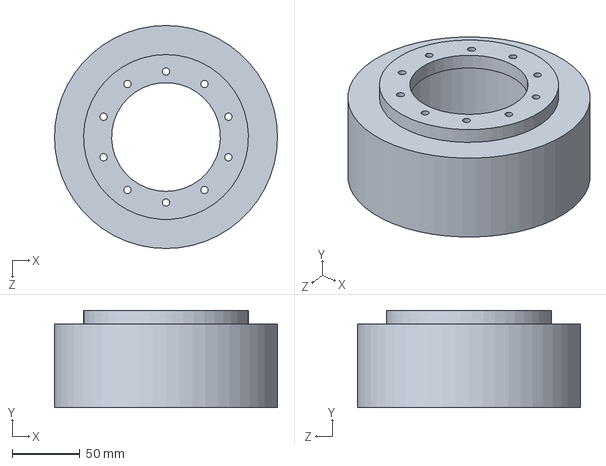
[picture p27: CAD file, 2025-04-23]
SolidWorks Files/Joint 1/J1 Motor Cover.SLDPRT
165.0 x 72.0 x 165.0 mm

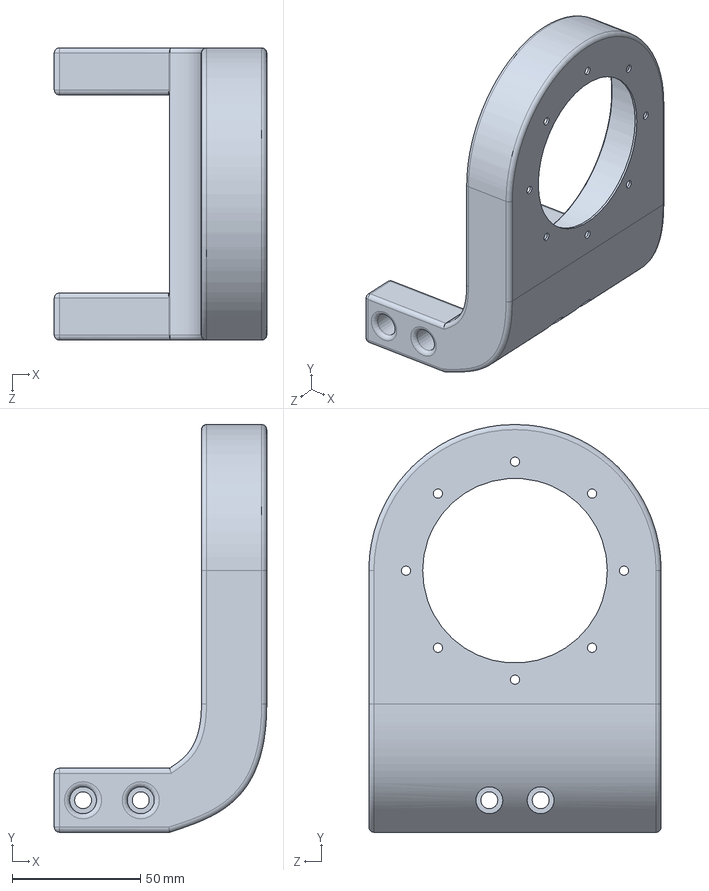
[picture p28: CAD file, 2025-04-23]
SolidWorks Files/Joint 3/J3 Motor Holder.SLDPRT
82.9 x 159.1 x 114.0 mm

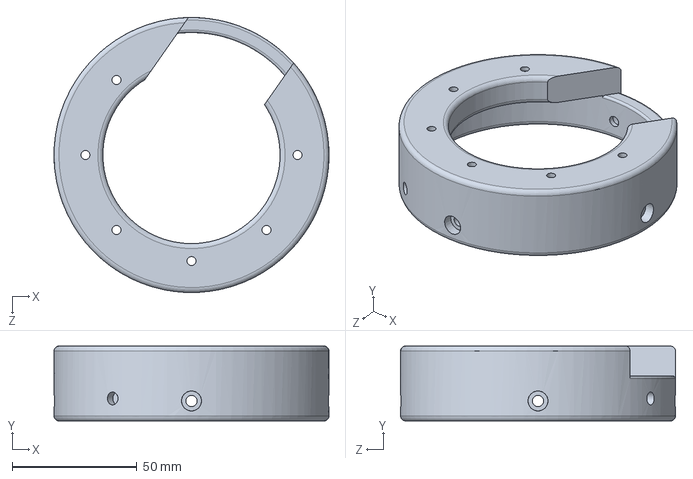
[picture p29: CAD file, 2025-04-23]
SolidWorks Files/Joint 4/J4 Motor Holder.SLDPRT
110.2 x 30.0 x 110.2 mm

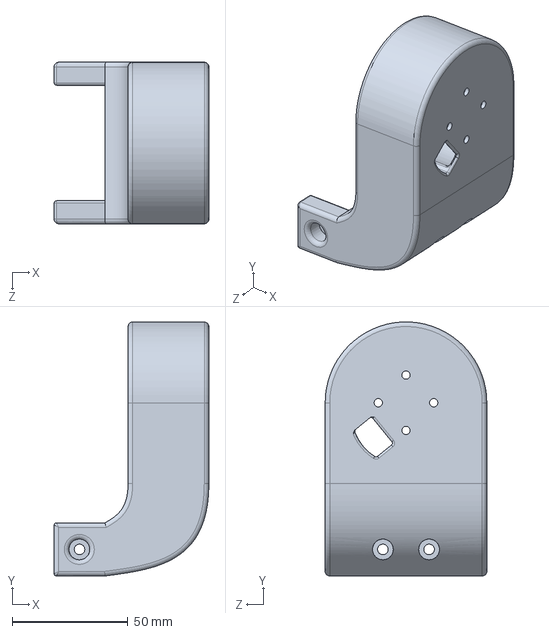
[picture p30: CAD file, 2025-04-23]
SolidWorks Files/Joint 5/J5 Motor Holder.SLDPRT
67.0 x 110.0 x 70.0 mm

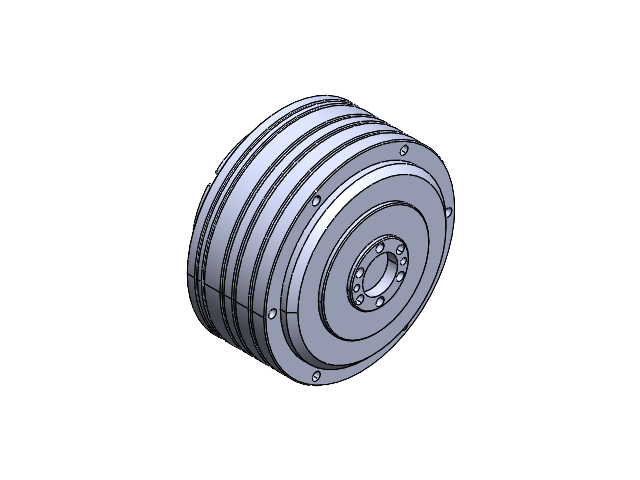
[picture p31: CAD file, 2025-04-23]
SolidWorks Files/Joint 1/J1 Motor (AK10-9 V2-0).SLDASM
AK10-9V2-0.stp
A80-6GZ.stp

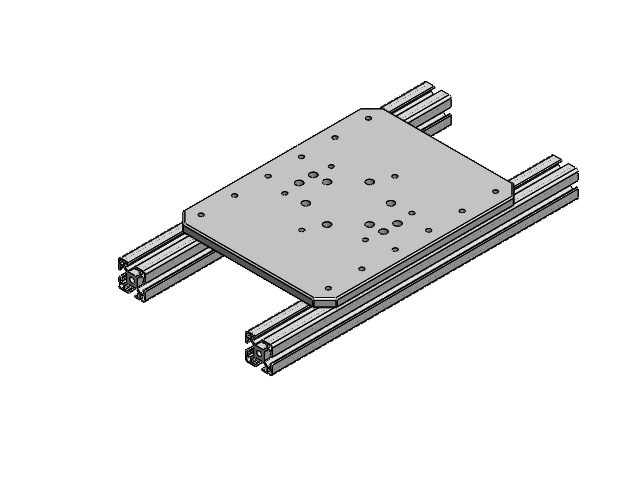
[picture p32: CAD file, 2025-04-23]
SolidWorks Files/Base/Robot Base Assembly w Alum Extrusions.SLDASM
Robot Base
Aluminum Extrusion (6575N202) x 2

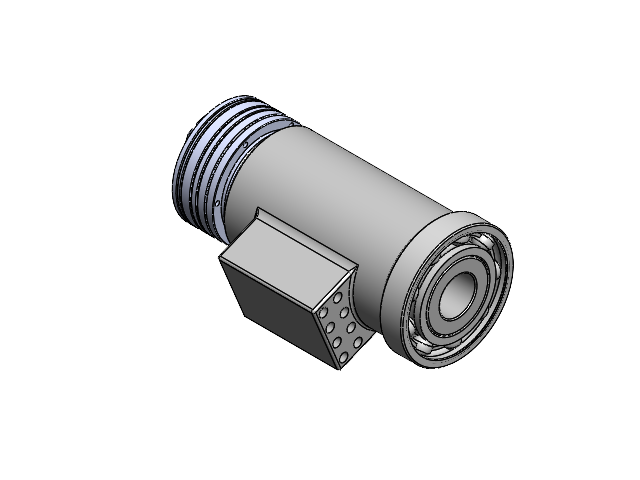
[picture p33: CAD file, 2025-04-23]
SolidWorks Files/Joint 2/J2Assembly.SLDASM
J2 Motor (AK10-9 V2-0)
J2 Ball Bearing (K972K3)
J2 Cylinder

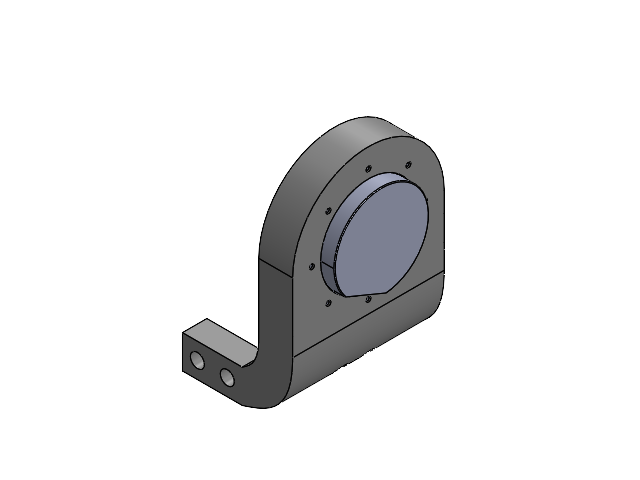
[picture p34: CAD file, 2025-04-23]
SolidWorks Files/Joint 3/J3 Motor Assembly.SLDASM
J3 Motor Holder
J3 Motor (AK80-6 & AK80-9)

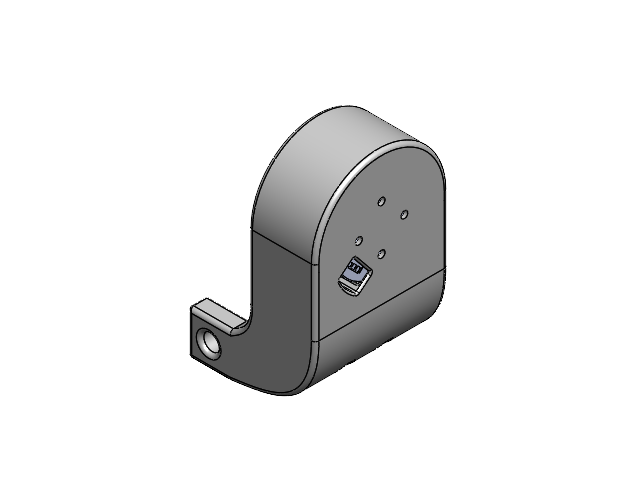
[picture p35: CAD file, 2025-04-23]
SolidWorks Files/Joint 5/J5 Motor Assembly.SLDASM
J5 Motor Holder
GL40_1_1.stp

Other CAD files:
SolidWorks Files/Joint 5/J5 Motor (GL40).SLDASM
SolidWorks Files/Joint 3/J3 Bearing Assembly.SLDASM
SolidWorks Files/Joint 5/J5 Bearing Assembly.SLDASM
SolidWorks Files/Joint 5/J5 Assembly.SLDASM
SolidWorks Files/5972K105_Ball Bearing.SLDPRT
SolidWorks Files/Base/Aluminum Extrusion (6575N202).SLDPRT
SolidWorks Files/Joint 1/J1 Motor Holder.SLDPRT
SolidWorks Files/Joint 1/J1 Mushroom Cap.SLDPRT
SolidWorks Files/Joint 2/J2 Bearing Holder.SLDPRT
SolidWorks Files/Joint 2/J2 Cylinder.SLDPRT
SolidWorks Files/Joint 2/J2 Motor (AK10-9 V2-0).SLDPRT
SolidWorks Files/Joint 2/J2 Motor Holder.SLDPRT
SolidWorks Files/Joint 3/Bicep.SLDPRT
SolidWorks Files/Joint 3/J3 Bearing Holder.SLDPRT
SolidWorks Files/Joint 3/J3 Cylinder.SLDPRT
SolidWorks Files/Joint 3/J3 Motor (AK80-6 & AK80-9).SLDPRT
SolidWorks Files/Joint 4/J4 Cross Roller Bearing (2010N14).SLDPRT
SolidWorks Files/Joint 4/J4 Motor Cover.SLDPRT
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

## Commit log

2025-03-28 Create SPRING 2025 MIDTERM REPORT.pdf
2025-04-23 Create 5972K105_Ball Bearing.SLDPRT
    [5972K105_Ball Bearing.SLDPRT]
2025-04-23 Create Aluminum Extrusion (6575N202).SLDPRT
    [Aluminum Extrusion (6575N202).SLDPRT]
2025-04-23 Create Robot Base Assembly w Alum Extrusions.SLDASM
    [Robot Base Assembly w Alum Extrusions.SLDASM]
2025-04-23 Create J2 Bearing Holder.SLDPRT
    [J2 Bearing Holder.SLDPRT]
2025-04-23 Create J2 Cylinder.SLDPRT
    [J2 Cylinder.SLDPRT]
2025-04-23 Create J2 Motor (AK10-9 V2-0).SLDPRT
    [J2 Motor (AK10-9 V2-0).SLDPRT]
2025-04-23 Create J2 Motor Holder.SLDPRT
    [J2 Motor Holder.SLDPRT]
2025-04-23 Create J2 Ball Bearing (K972K3).SLDPRT
    [J2 Ball Bearing (K972K3).SLDPRT]
2025-04-23 Create J3 Bearing Assembly.SLDASM
    [J3 Bearing Assembly.SLDASM]
2025-04-23 Create J3 Bearing Holder.SLDPRT
    [J3 Bearing Holder.SLDPRT]
2025-04-23 Create J3 Cylinder.SLDPRT
    [J3 Cylinder.SLDPRT]
2025-04-23 Create J3 Motor (AK80-6 & AK80-9).SLDPRT
    [J3 Motor (AK80-6 & AK80-9).SLDPRT]
2025-04-23 Create J3 Motor Assembly.SLDASM
    [J3 Motor Assembly.SLDASM]
2025-04-23 Create J3 Motor Holder.SLDPRT
    [J3 Motor Holder.SLDPRT]
2025-04-23 Create 4471N14_Face-Mount Crossed-Roller Bearing.SLDPRT
2025-04-23 Create J4 Cross Roller Bearing (2010N14).SLDPRT
    [J4 Cross Roller Bearing (2010N14).SLDPRT]
2025-04-23 Create J4 Motor Assembly.SLDASM
2025-04-23 Create J4 Motor Cover.SLDPRT
    [J4 Motor Cover.SLDPRT]
2025-04-23 Create J4 Motor Holder.SLDPRT
    [J4 Motor Holder.SLDPRT]
2025-04-23 Create J4 Mushroom Cap.SLDPRT
    [J4 Mushroom Cap.SLDPRT]
2025-04-23 Create J5 Assembly.SLDASM
    [J5 Assembly.SLDASM]
2025-04-23 Create J5 Bearing (5972K105).SLDPRT
    [J5 Bearing (5972K105).SLDPRT]
2025-04-23 Create J5 Bearing Assembly.SLDASM
    [J5 Bearing Assembly.SLDASM]
2025-04-23 Create J5 Bearing Holder.SLDPRT
    [J5 Bearing Holder.SLDPRT]
2025-04-23 Create J3 Ball Bearing (5972K113).SLDPRT
    [J3 Ball Bearing (5972K113).SLDPRT]
2025-04-23 Create J5 Cylinder.SLDPRT
    [J5 Cylinder.SLDPRT]
2025-04-23 Create J5 Motor (GL40).SLDASM
    [J5 Motor (GL40).SLDASM]
2025-04-23 Create J5 Motor Assembly.SLDASM
    [J5 Motor Assembly.SLDASM]
2025-04-23 Create J5 Motor Holder.SLDPRT
    [J5 Motor Holder.SLDPRT]
2025-04-23 Create J5 Cylinder Cap.SLDPRT
    [J5 Cylinder Cap.SLDPRT]
2025-04-23 Create LANL Robot Assembly.SLDASM
2025-04-23 Create J1 Mushroom Cap.SLDPRT
    [J1 Mushroom Cap.SLDPRT]
2025-04-23 Create J1 Motor Holder.SLDPRT
    [J1 Motor Holder.SLDPRT]
2025-04-23 Create J1 Motor Cover.SLDPRT
    [J1 Motor Cover.SLDPRT]
2025-04-23 Create J1 Motor (AK10-9 V2-0).SLDASM
    [J1 Motor (AK10-9 V2-0).SLDASM]
2025-04-23 Create J1 Cross Roller Bearing (2010N16).SLDPRT
2025-04-23 Create Robot Base.SLDPRT
    [Robot Base.SLDPRT]
2025-04-24 Create Final Organized BOM.xlsx
    [Final Organized BOM.xlsx]
2025-04-24 Create LANL Human Robotic Arm Attachment Showcase Poster.pdf
2025-04-24 Create Assembly Manual.pdf
2025-04-24 Create Analytical Graph of Motor Operation.png
2025-04-24 Create Motor Image.png
2025-04-24 Create Motor Dimensions.png
2025-04-29 Create Texas A&M Human Robotic Arm Attachment.mp4
2025-04-29 Create Motor Pics.pdf
2025-04-29 Create SPRING 2025 FINAL REPORT.pdf
2025-04-29 Create Motor Specs.pdf
